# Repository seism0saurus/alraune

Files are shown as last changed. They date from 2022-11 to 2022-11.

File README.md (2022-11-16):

# Alraune mit Bewässerung (Work in Progress)

Dieses Repository enthält den Quellcode für einen D1 Mini, die Assets und Informationen für Bau einer schreienden Alraune mit Wasserpumpe.

Das Repository ist noch nicht ganz fertig.

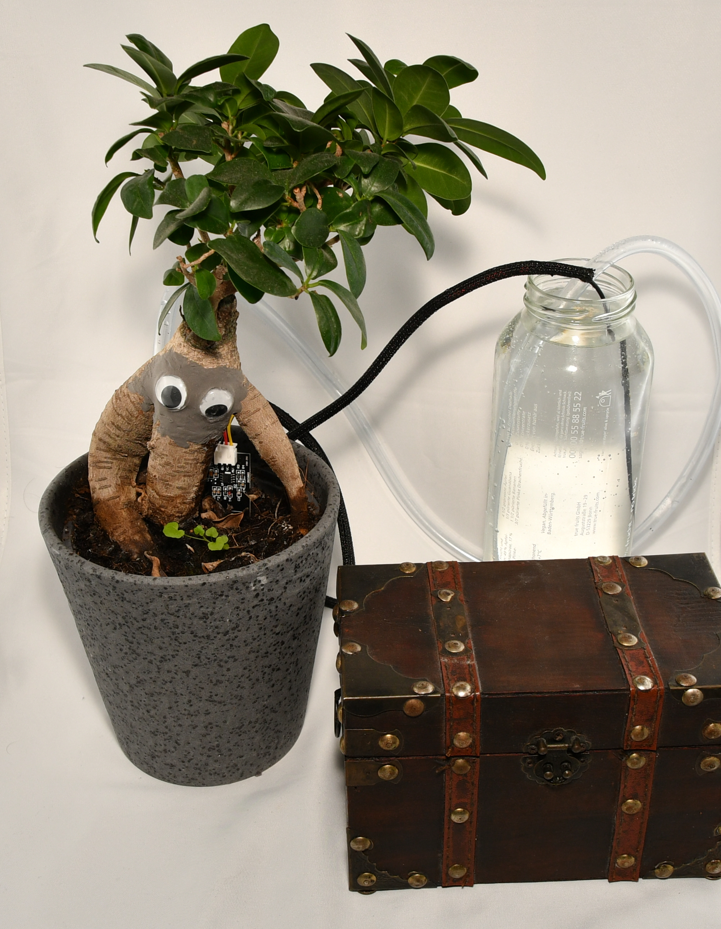
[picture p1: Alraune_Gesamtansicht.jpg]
Gesamtansicht der Araune bestehend aus Ginseng, Kiste mit Schaltung und Wassertank


## Funktionen

- Automatisches Wässern, wenn die Alraune trocken wird
- Akkustiche Erinnerung mit verschiedenen Sprüchen, den Wasserbehälter der Pumpe nachzufüllen
- Übermittlung statistischer Daten inkl. Feuchtigkeit der Erde an einen konfigurierbaren Logstashserver (Eigener ELK Stack benötigt)
  - Dashboard mit aktuellen Werten und zeitlichem Verlauf
  - Alarmfunktion über Kibana
- Setup Funktion
  - Aufspannen eines Access Points mit WLAN alraune und Passwort
  - Bereitstellen einer Setupseite unter http://alraune.local im alraune WLAN
  - Konfiguration von SSID und WLAN Passwort und Name der Alraune
  - Ladebildschirm
  - Automatische Weiterleitung zur Statusseite, wenn das Setup erfolgreich war
- Statusseite unter http://alraune.local im konfigurierten WLAN
  - Alraune zum Kitzeln
  - Statusinformationen zu Feuchtigkeit und ob die Alraune Wasser braucht oder der Container aufgefüllt werden muss
  - Möglichkeit den Sensor neu zu kalibrieren
  - Einstellung der Lautstärke der Sounds
  - Abspielen der Sounds für Demozwecke
- Konfigurierbare automatische Upgrades (Funktionen müssen auf eigenem Server implementiert sein)
  - Installation neuer signierter Versionen der Firmware
  - Aktualisierung der Dateien des Dateisystems
  - Löschen nicht mehr benötigter Dateien

## Anleitung

Eine detaillierte Anleitung wird in mehreren Beiträgen auf meinem Blog seism0saurus.de erscheinen:
 - [Teil 1 - Überblick](https://seism0saurus.de/posts/alraune/)

### Komponenten verbauen

Die Schaltung habe ich nachträglich mit [Fritzing](https://fritzing.org/) visualisiert. Das OpenSource Tool kann man gegen eine Gebühr herunterladen oder selbst kompilieren und bietet einen visuelleren Zugang als reine Schaltpläne. Bei größeren Installationen wird es aber unübersichtlich.

Bitte prüft vor dem Bau, ob die abgebildete Schaltung für eure Auswahl an Komponenten korrekt ist und holt euch gegebenenfalls jemand mit Erfahrung zur Unterstützung. Ich übernehme keine Garantie für einen gefahrlosen Betrieb auf Basis dieser Repositories oder der Blogbeiträge.

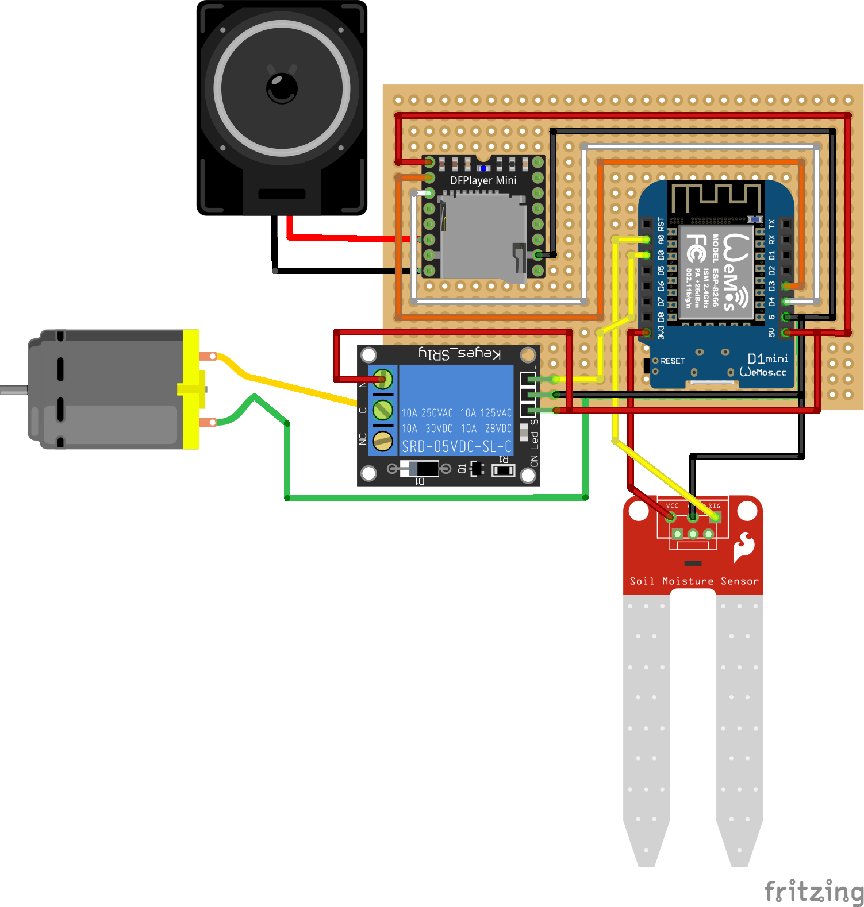
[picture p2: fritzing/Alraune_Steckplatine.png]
Steckplatinenbild aller Komponenten der Araune


### IDE intallieren und einrichten

Das Projekt habe ich in der Arduino IDE entwickelt. Vermutlich läuft es auch in anderen IDEs, aber ich nutzte z.b. die Funktion zum Signieren von Upgrades.

#### IDE installieren

Lade die IDE einfach von der [Projektseite](https://www.arduino.cc/en/software) herunterladen. Es gibt sie für Windows, Linux und MacOS.

#### ESP8266 Library installieren

Da sich im [Arduino](https://github.com/esp8266/Arduino/) Code des ESP8266 Projekts ein [Bug](https://github.com/esp8266/Arduino/issues/8707) bei der Prüfung der Signaturen beim Upgrade eingeschlichen hatte, muss momentan die Bibliothek aus dem master Branch genutzt werden. Dort ist ein [Pull Request](https://github.com/esp8266/Arduino/pull/8709) von mir gemerged worden.

Nach dem nächsten Release kann die normale Releaseversion über den Boardmanager installiert werden.

Die Installation ist in einzelnen Schritten in der [Dokumentation](https://arduino-esp8266.readthedocs.io/en/latest/installing.html#using-git-version) des Projekts nachzulesen.

### Schlüsselpaar erstellen

Aus dem entsprechenden [Abschnitt der Dokumentation](https://arduino-esp8266.readthedocs.io/en/latest/ota_updates/readme.html#signed-binary-prerequisites) des ESP8266 Projekts ist zu entnehmen, dass 2048 Bit lange RSA Schlüssel für die Signatur der Upgrades genutzt werden können.

Bei einem Upgrade prüft der Controller dann mit dem öffentlichen Schlüssel, ob die geladene Datei vom privaten Schlüssel signiert wurde. So ist sichergestellt, dass keine gefälschten Upgrades installiert werden.

Unter Linux kann ein passendes Schlüsselpaar im Ordner [Alraune](./Alraune/) wie folgt angelegt werden.

```bash
cd /path/to/repo/Alraune
openssl genrsa -out private.key 2048
openssl rsa -in private.key -outform PEM -pubout -out public.key
```

#### Automatisches Signieren

Solange das Schlüsselpaar in dem Ordner liegt und man richtiges Betriebsystem (Linux, MacOS) nutzt, wird die Arduino IDE [Autosigning](https://arduino-esp8266.readthedocs.io/en/latest/ota_updates/readme.html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) aktivieren.

Damit automatisch die signierte Version exportiert wird, kann die `platform.txt` des ESP8266 überschrieben werden.
Dazu muss die Datei [platform.local.txt](./platform.local.txt) in den Ordner der Library `esp8266` kopiert werden.

Wenn wie hier die Library über git installiert wurde, sollte folgender Befehl ausreichen.
```bash
cd /path/to/repo/
cp platform.local.txt ~/Arduino/hardware/esp8266com/esp8266/
```

Dadurch wird beim Export der Binärdatei in der Arduino IDE über `Sketch -> Kompilierte Binärdatei Exportieren` die signierte Datei exportiert und nicht die unsignierte.

#### Manuelles Signieren

Unter Windows muss man die kompilierten Upgrades manuell signieren. Für die Prüfung muss der Publik Key mit in den [data](./data/) Ordner abgelegt werden.

Danach muss in der [Alraune.ino](./Alraune/Alraune.ino?plain=1#L72) Datei die Variable `MANUAL_SIGNING` auf 1 gesetzt werden.

```c
#define MANUAL_SIGNING 1
```
Dadurch wird automatisch der `public.key` vom Filesystem des D1 Mini geladen und zur Prüfung der Upgradedateien genutzt.

Dieser Prozess wird auch in der [Dokumentation](https://arduino-esp8266.readthedocs.io/en/latest/ota_updates/readme.html#manual-signing-of-binaries) des ESP8266 Projekts beschrieben.

### Konfiguration anpassen

In der [config.json](./data/config.json) müssen die Parameter für den Upgradeserver und den Logstashserver gesetzt werden.

Außerdem sollte die Uhrzeit eingestellt werden, wann die Alraune schreien soll. Standardmäßig schreit sie von stündlich von 8 - 22 Uhr.

Den Namen der Alraune, den Geburtstag und die Zugangsdaten zum WLAN werden während des Setups erfasst und müssen nicht gesetzt werden.

### Filesystem vorbereiten

Es gibt ein Plugin für die Arduino IDE, mit der Dateien auf das Filesystem des D1 Mini übertragen werden können.

#### Plugin installieren

Zunächst muss das Plugin von der [Projektseite](https://github.com/earlephilhower/arduino-esp8266littlefs-plugin/releases) heruntergeladen werden. Danach ist die Installation wie im [ESP8266 Projekt](https://arduino-esp8266.readthedocs.io/en/latest/filesystem.html#uploading-files-to-file-system) beschrieben.

#### Dateien zippen und kopieren

Damit die Dateien für den Webserver weniger Platz verbrauchen, habe ich ein kleines [Skript](./import_data.sh) geschrieben, dass die statischen Dateien mit gzip komprimiert. Es kopiert die Dateien aus dem [data](./data/) Ordner des Repositories in den [data](./Alraune/data) des Arduino Projekts.

Das Skript kann einfach in der Konsole unter Linux ausgeführt werden.
```bash
cd /path/to/repo/
./import_data.sh
```

#### Dateien hochladen

Der D1 Mini muss über USB mit dem Rechner verbunden sein und es darf **kein** Serieller Monitor geöffnet sein.

Wenn alle Dateien im Ordner [data](./Alraune/data) des Arduino Projekts liegen, können sie über das Menü `Werkzeuge -> ESP8266 LittleFS Data Upload` auf den D1 Mini hochgeladen werden.

### MicroSD Karte vorbereiten

Den Inhalt des Ordners [sd_card](./sd_card/) muss in der richtigen Reihenfolge auf eine MicroSD Karte kopiert werden, da der DFPlayer Mini nicht die Dateinamen, sondern die Reihenfolge der Erstellung beachtet.

Daher sollte die Karte frisch mit FAT32 formatiert werden und dann mit dem Dateiexplorer unter Windows oder mit rsync unter Linux kopiert werden.
Danach sollten sich auf der Karte nur die Ordner 01-03 befinden.

### Code kompilieren

In der Arduino IDE auf `Sketch -> Überprüfen/Kompilieren` klicken.

### Logstash konfigurieren

TBD

### Upgradeserver konfigurieren

TBD

### Flashen

Der D1 Mini muss über USB mit dem Rechner verbunden sein.

In der Arduino IDE auf `Sketch -> Hochladen` klicken.

### Upgrades

In der Arduino IDE auf `Sketch -> Kompilierte Binärdatei Exportieren` klicken.

Bei manuellen signieren die Datei anschließen signieren.

Falls der Upgrade Server so konfiguriert ist wie meiner (Anleitung folgt), kann das Skript [import_data.sh](./import_data.sh) genutzt werden. Hierfür ist ein konfigurierter SSH Zugang zum Upgradeserver nötig.

Dann sollten zunächst die aktuellen Daten kopiert werden und danach das Skript  in der Konsole unter Angabe einer neuen Versionsnummer unter Linux ausgeführt werden.
```bash
cd /path/to/repo/
./import_data.sh
./import_data.sh 0.9.11
```

Es wählt sich über ssh auf dem Upgradeserver ein, legt im Homerverzeichnis unter `esp-update-server/projects/alraune` einen neuen Ordner für die angegebene Versionsnummer an und kopiert die neue Firmware und die Daten aus dem Ordner [data](./Alraune/data) des Arduino Projekts.

Die Alraune prüft automatisch nach einigen Minuten nach neuen Updates und lädt diese herunter, wenn die Versionsnummer größer ist, als die aktuell eingesetzte.

## Feedback

Gerne könnt ihr hier auf GitHub Fehler melden oder Verbesserungen einreichen. Auch sonstiges konstruktives Feedback ist mit sehr Willkommen. Dies ist mein erstes richtiges IoT Projekt und ich lerne gerne dazu.

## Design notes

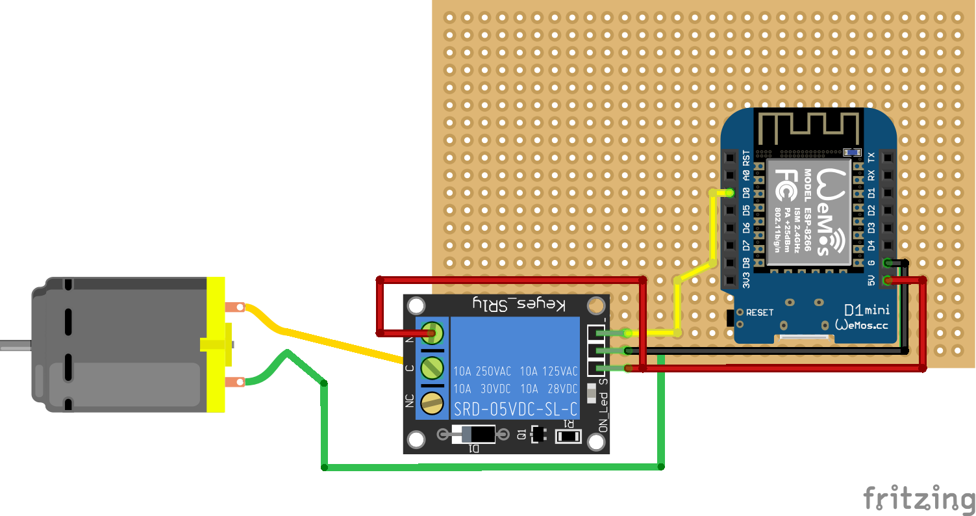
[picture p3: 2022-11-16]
fritzing/Pumpe_Steckplatine.png

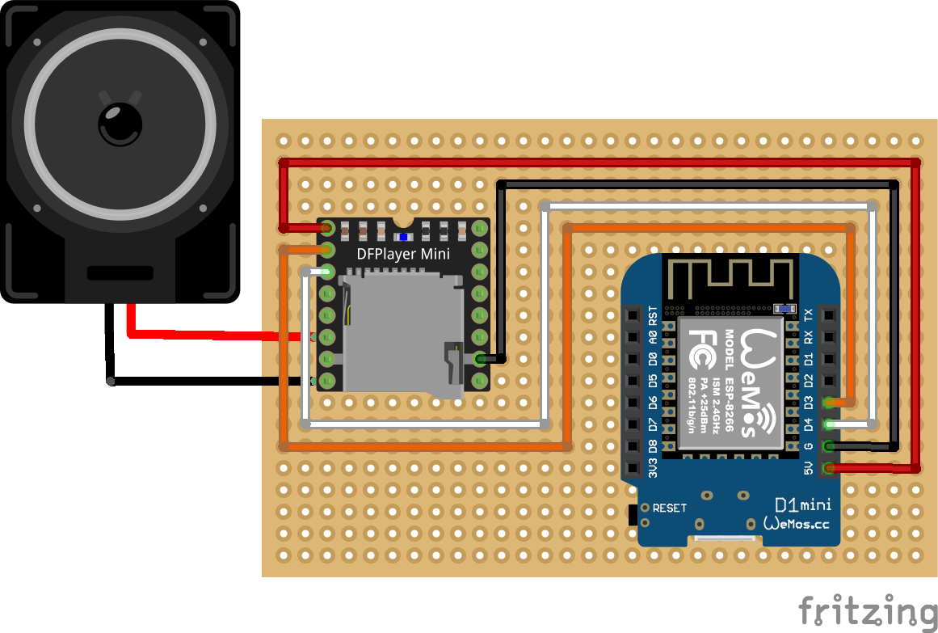
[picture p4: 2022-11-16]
fritzing/Audioplayer_Steckplatine.png

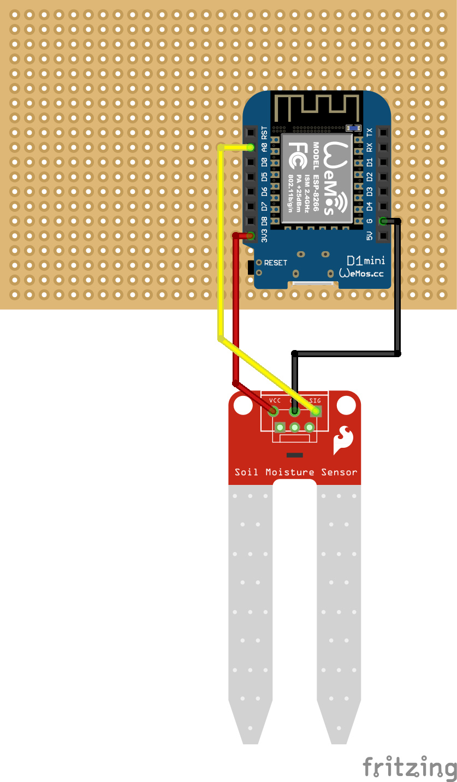
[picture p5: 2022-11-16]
fritzing/Feuchtigkeitssensor_Steckplatine.png

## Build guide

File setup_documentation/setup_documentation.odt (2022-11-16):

1 - Connect the Cable | 2 - Connect to WLAN | 3 - Start the Setup

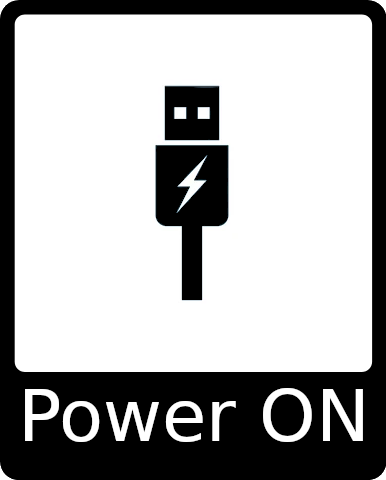
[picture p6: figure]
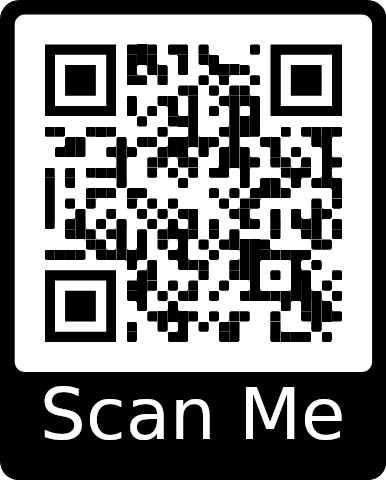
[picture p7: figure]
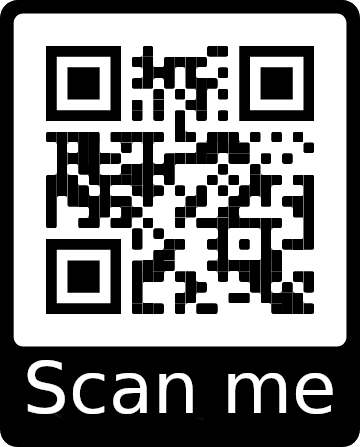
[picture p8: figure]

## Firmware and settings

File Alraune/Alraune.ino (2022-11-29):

/*
 * Pump control with moisture sensor.
 * Needs
 * - a moisture sensor with max 3V output on the data channel
 * - a relay for 5V 
 * - a water pump for 5V
 * - and a DFPlayer mini
*/


/*
 * Inclusion of libraries
 * 
 * We need ESP8266WiFi for wireless lan connectivity
 * ESP8266mDNS is used for broadcasting of the domain alraune.local
 * ESP8266WebServer is our webserver, that handles the homepage, json output of the status and parses commands from the setuppage or homepage
 * CertStoreBearSSL is used for secure connection to servers and validation of upgrades
 * ESP8266HTTPClient is used to send log messages to a logserver
 * FS and LittleFS are used for storage the images, config files and the homepage files
 * time and millisDelay is for asynchronous handling of timeouts for the pump
 * SoftwareSerial and DFRobotDFPlayerMini are used for the audio playback
 * ESP8266httpUpdate is used for OTA upgrades of the system
 * Arduino_JSON is used for parsing or writing structured data like the config file or POST requests
 */
#include <ESP8266WiFi.h>
#include <ESP8266mDNS.h>
#include <ESP8266WebServer.h>
#include <CertStoreBearSSL.h>
#include <ESP8266HTTPClient.h>
#include <FS.h>
#include <LittleFS.h>
#include <time.h>
#include <millisDelay.h>
#include <SoftwareSerial.h>
#include <DFRobotDFPlayerMini.h>
#include <ESP8266httpUpdate.h>
#include <Arduino_JSON.h>

/* 
 * Hide passwords in log lines
 * Set to false for debugging of connection problems
 */
constexpr boolean HIDE_PASSWORDS = true;

/* 
 * Upgrade configuration
 * 
 * The version is used to request upgrades from the upgrade server. If a newer version is available, the upgrade is send to the device and installed after verification
 * The upgrade URL is the hostname of the upgrade server. This is configured in the config.json. This system requires it to have a TLS secured http server on port 443
 * The upgrade path is the path to the project folder on the upgade server. On my upgrade server this is /alraune/files/
 * A complete request for the new firmare could be https://my-upgrade-server.org/alraune/files/firmware.bin
 * The upgrade user and password are needed for the basic authentication against the upgrade server. Since the firmware could contain sensitive information like credentials, they should be protected
 */
#ifndef VERSION
  #define VERSION "0.9.13"
#endif
String upgradeUrl;
String upgradePath;
String upgradeUser;
String upgradePassword;

/* 
 * Code signing
 * 
 * The Alraune uses automatic code signing and verification with the Arduiono IDE
 * See https://arduino-esp8266.readthedocs.io/en/latest/ota_updates/readme.html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
 * If you want to sign the files manually or you don't have access to a good operating system, you can enable the manual mode.
 * Set MANUAL_SIGNING to 1 and provide the public key on the LittleFS
 */
#ifndef MANUAL_SIGNING
  #define MANUAL_SIGNING 0
#endif
#if MANUAL_SIGNING
  BearSSL::PublicKey *signPubKey = nullptr;
  BearSSL::HashSHA256 *hash;
  BearSSL::SigningVerifier *sign;
#endif

/*
 * WLAN configuration
 * 
 * Stores the SSID and the password to access the network
 * Both settings are read from the config.json from the LittleFS
 * After the startup the Alraune tries to connect to the configured WLAN
 * If the connection succeeds, the connectedToSsid is set to true and the complete system is started
 * If the connection fails, the connectedToSsid is set to false and only the needed parts are started to provide a setup page in the alraune WLAN under http://192.168.4.1/
 * The string wlanListJson will contain the JSON of the found wireless networks
 */
String ssid;
String wlanPassword;
boolean connectedToSsid = false;
byte consecutiveErrors = 0;
String wlanListJson;

/*
 * HTTP client
 * 
 * Uses the secure HTTP client by BearSSL. It can access TLS encrypted webservers
 * The ca certificate as trust ancor is read from the LittleFS file ca.cer
 */
BearSSL::WiFiClientSecure client;

/*
 * Filesystem configuration
 * 
 * Configure a LittleFS filesystem to read and store config files and ressources for the webserver
 */
FS* fileSystem = &LittleFS;
LittleFSConfig fileSystemConfig = LittleFSConfig();
boolean fsOK;

/*
 * Media player configuration
 * 
 * Configure a serial interface on the pins 4 and 5 and initialize the conncted DFPlayer
 * The folder variables define wich folder number on the DFPlayer MiniSD card should be used for which purpose
 * They are important for the order in which you store the files on the card. See https://wiki.dfrobot.com/DFPlayer_Mini_SKU_DFR0299#target_6
 * - WATER_REFILL_FOLDER contains the sounds, that should remind the owner to refill the water. The number of this sounds will be stored in waterRefillSounds
 * - BIRTHDAY_FOLDER contains the sounds, that are played on the configured birthday of the owner. The number of this sounds will be stored in birthdaySounds
 * - CHRISTMAS_FOLDER contains the sounds, that are played on christmas eve (24.12). The number of this sounds will be stored in christmasSounds
 */
SoftwareSerial audioSerial(D2, D1); // RX, TX
DFRobotDFPlayerMini myDFPlayer;
uint8_t volume = 10;
constexpr uint8_t WATER_REFILL_FOLDER = 1;
constexpr uint8_t BIRTHDAY_FOLDER = 2;
constexpr uint8_t CHRISTMAS_FOLDER = 3;
uint8_t waterRefillSounds = 0;
uint8_t birthdaySounds = 0;
uint8_t christmasSounds = 0;

/* 
 *  Webserver configuration
 *  
 *  Configure an ESP webserver on port 80
 *  The ip will be stored in the ip variable
 *  The hostname will be read from the config.json file and defines name of the webpage. The suffix .local will be appended since we use mDNS
 *  The pagename will be read from the config.json and is configured during setup. This will be the title of the homepage shown in the browser
 *  TEXT_PLAIN and APPLICATION_JSON are used for mimetypes
 */
constexpr int port = 80;
ESP8266WebServer server(port);
String ip;
String hostname;
String pagename;
const char TEXT_PLAIN[] PROGMEM = "text/plain";
const char APPLICATION_JSON[] PROGMEM = "application/json";

/*
 * Pin configuration
 * 
 * Configure which pins are used for the sensor and actuator as well as the led
 * The sensorPin is connected to the moisture sensor and should not get more than 1V (pure ESP) or 3V (D1 Mini)
 * The relayPin is the pin that controls the realay to power the water pump
 * The led is used to signal access to the webserver, pump activation or upgrades
 */
constexpr int sensorPin = A0;
constexpr int releayPin = D0;
constexpr int led = LED_BUILTIN;

/* 
 *  Logging configuration
 *  
 *  Configure the URL and credentials for the logserver
 *  The logUrl is the complete URL that can consume json log events like logstash. This can be configured through config.json
 *  The variables logUser and logPassword contain the credentials to the logserver
 *  Since you can write events to the server, it should be protected by TLS and basic auth. These are configured through config.json
 */
String logUrl;
String logUser;
String logPassword;


/* 
 * Business variables
 * 
 * Variables that are actually used for calculations of water usage, moisture and activation of the water pump
 * The sensorThreshold will be overridden with the value from config.json and can be recalibrated on the homepage
 * The sensorValue will store the actual value of the moisture sensor
 * The variable needsWater is set to true, if the earth is too dry. Otherwise it is false
 * The variable needsRefill is set to true, if the water container needs to be refilled. Otherwise it is false
 * The variables birthdayDay and birthdayMonth store the birthday of the owner. They will be configured during the setup process and stored in the config.json. The Alraune will sing for the owner on his or her birthday
 * The variables CHRISTMAS_DAY and CHRISTMAS_MONTH store the day, when the Alraune will sing christmas songs or say nice things to the owner
 * The variables fromHour and toHour sotre the time range, in wich the Alraune will make sounds. It will stay silent in the hours outside that range
 */
int sensorThreshold = 380;
int sensorValue = 0;
boolean needsWater = false;
boolean needsRefill = false;
uint8_t birthdayDay = 22;
uint8_t birthdayMonth = 11;
constexpr uint8_t CHRISTMAS_DAY = 24;
constexpr uint8_t CHRISTMAS_MONTH = 12;
uint8_t fromHour = 8;
uint8_t toHour = 22;

/* 
 * Delays
 * 
 * The delays are used to run functions after a fixed time or regularly
 * The pumpDelay is started, when the moisture of the earth is too low. After 10 seconds the pump is stopped again
 * The moistureDelay is started at the same time as the pumpDelay but runs one hour. If the earth is still to dry after that time, we can assume, that there was not enough water in the water container and we inform the owner
 * The networkMonitoringDelay ist started, when a network error occurs. After 10 seconds we check the connectivity to the WLAN and restart the network, if we still don't have a connection
 * The logDelay is used to send a statistic log event to the logserver every minute
 * The easterEggDelay runs every hour and plays a birthday or christmas sound, if it is the correct date and time
 * The upgradeDelay is used to check for upgrades every 10 minutes
 */
millisDelay pumpDelay;
millisDelay moistureDelay;
millisDelay networkMonitoringDelay;
millisDelay logDelay;
millisDelay easterEggDelay;
millisDelay upgradeDelay;

/*
 * Setup method to prepare the Alraune
 * 
 * After an inial delay, the pins and the serial interface of the D1 mini are initialized. After this stage we can see log messages through the serial interface
 * The next stage initializes the filesystem LittleFS, since we need the config file and the certificate for the rest of the setup
 * Now we can load the configuration from the config.json file.
 * 
 * After we loaded the config we can try to setup the network. First the Alraune tries to connect to the WLAN from the config.json.
 * If it fails to connect multuple times it opens an Access Point with a WLAN called alraune and listens on the IP 192.168.4.1
 * If the connection to the configured network works, no Acces Point is started and the Alraune gets an IP from the DHCP server and announces its name alraune.local through mDNS
 * After the network is running in one of the two modes, the HTTP server is started
 * The server will deliver either the setup page, if it runs in AP mode, or the homepage of the Alraune.
 * To finish the setup got to the WLAN alraune and open http://192.168.4.1 in your browser
 * 
 * Only if the Alraune could connect to your configured WLAN it starts the other features
 * 
 * The logging is responsible for sending regular statistics to the logserver, where the data can be visualized and processed for alarms or other stuff
 * Furthermore it can send errors or important logs to the logserver
 * The certiicate of the CA of the logserver has to be saved as ca.cer in the LittleFS. The let's encrypt certificate is preconfigured 
 * 
 * After the logging is enabled, the DFPlayer mini is initialized through the software serial
 * The volume is set to the configured value and the number of sounds is determined. This is later used to play a random sound
 * 
 * After that the clock is synchronized with a time server over NTP. The correct time is needed for verification of TLS certificates or other signatures
 * Furthermore we need the date to check the birthday and christmas easter eggs
 *  
 * When the clock is synchronized the easter eggs can be handled. On the birthday of the owner an on christmas eve the Alraune will play some special sounds
 * 
 * At last the upgrade delay is started. Every 10 minutes the Alraune will connect to the configured upgrade server and sends the current version
 * If a newer versino is available the files on the LittleFS and the firmware will be updated. After that the system automatically reboots
 */
void setup() {
  delay(1000);
  setupPins();
  setupSerial();
  setupFs();
  loadConfigFromFs();
  setupNetwork();
  setupServer();
  if (connectedToSsid){
    setupLogging();
    setupDFPlayer();
    setupClock();
    setupEasterEggs();
    setupUpgrade();
    Serial.println(F("Finished setup. Please go to http://alraune.local to view the dashboard"));
  } else {
    Serial.println(F("Finished setup. Please connect to 'alraune' WLAN with password 'WaterIsLive' and go to http://alraune.local to finish configuration"));
  }
  log("Setup finished");
}


/*
 * The loop method for the execution of the application
 * 
 * When the setup is not finished and therefore there is no network connectivity, the Alraune will only serve the setup page
 * After the setup is finished AND eherefore the Alraune is in your wireless network, the homepage is served and all the features are handled
 * 
 * The alraune will publish it's name alraune.local through mDNS
 * 
 * The moisture is checked and the pump will be activated, if needed
 * 
 * If the pump was active and the earth is still too dry, the owner will be informed via sounds by the Alraune
 * 
 * The media player handler will get the status from the DFPlayer and print error messages
 * 
 * The eeaster egg handler will play a special sound every hour during birthdays and christmas eve
 * 
 * The upgrade function checks if a newer version is available on the upgrade server and perfomse the upgrade
 * 
 * The logger sends the current status to the log server for further processing
 * 
 * If any network errors were detected, the network is reconnected by the network error handler
 */
void loop() { 
  handleHttpRequests();
  updateDns();
  if (connectedToSsid){
    activatePumpIfPlantIsDry();
    warnHumanIfPlantisStillDry();
    handleMediaPlayer();
    handleEasterEggs();
    upgrade();
    logStatus();
    handleNetworkErrorsIfNeeded();
  }
}

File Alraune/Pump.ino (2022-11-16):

/*
 * Activate the water pump if needed
 * 
 * This method checks the current moisture value from the external sensor and starts the pump, if it is too dry
 * Delays are used to control the duration of the pumping and when the next test should be made
 */
void activatePumpIfPlantIsDry(){
  // The sensor ranges from 0-1000. The value is higher, if the soil is more dry. Invert the value, since we want to measure moisture not dryness
  sensorValue = 1000 - analogRead(sensorPin);
  
  if (sensorValue < sensorThreshold){
    needsWater = true;
    if (!pumpDelay.isRunning() && !moistureDelay.isRunning()){
      Serial.println(F("Plant needs water. Starting pump"));
      digitalWrite(releayPin, LOW);
      pumpDelay.start(10000);
      moistureDelay.start(3600000);
    }
  } else {
    needsWater = false;
  }
  
  if (pumpDelay.justFinished()){
    Serial.println(F("Pump delay finished. Stopping pump"));
    digitalWrite(releayPin, HIGH);
  }
}

/*
 * Warn owner if the plant is too dry after the pump was active
 * 
 * Plays a random water refill sounds when the delay is finished and the earth is still to dry
 * We D1 Mini has only one analog input, so we can't use a second sensor to check, if there is still water in the water container
 * Therefore I assume that the moisture level will go up a lot, if water got pumped into the earth
 * If thats not the case, the water must be empty or the tube is no longer in the plant
 */
void warnHumanIfPlantisStillDry(){
  // The sensor ranges from 0-1000. The value is higher, if the soil is more dry. Invert the value, since we want to measure moisture not dryness
  sensorValue = 1000 - analogRead(sensorPin);

  // if the water still needs water, the water tank has to be refilled
  if (moistureDelay.justFinished()){
    if (sensorValue < sensorThreshold){
      Serial.println(F("Moisture delay finished. Planed still needs water. Human has to refill"));
      if (isInHours()){
        playWaterRefillSound();
      }
      needsRefill = true;
    } else {
      Serial.println(F("Moisture delay finished. Planed has enough water. Nothing to do"));
      needsRefill = false;
    }
  } else {
    delay(1);
  }
}
